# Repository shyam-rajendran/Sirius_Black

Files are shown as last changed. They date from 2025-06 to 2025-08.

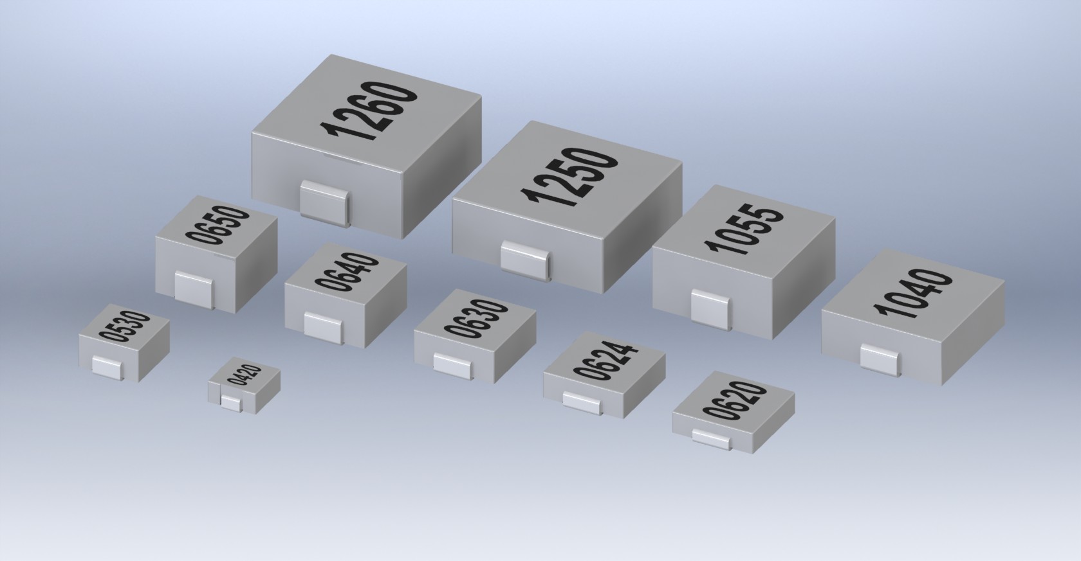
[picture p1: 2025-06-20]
3D Models/SMD Inductors/Inductors.JPG

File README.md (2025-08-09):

# Sirius Black - Flight Computer
<p align="center">
   &nbsp;&nbsp;&nbsp;
  
</p>

Sirius Black is the 5th gen custom flight computer fully designed and developed in house for the sounding rocket built for IREC 25, Airavata. 

Sirius Black consists a multitude of sensors required but not limited for model rocketry, along with 2 integrated pyro channels and 4 servo channels for any actuator control operations. ESP32-S3-N4R8 was the chosen microcontroller due to its great functionalities and prior familiarity with the ESP32 family ICs.

The following write up gives a comprehensive data that could be used while operating with Sirius Black for future projects or serve as reference for any future developements. 

Throughout the developement of this, I documented my approach and considerations I took for most of the steps involved in component selection, schematic design, layout planning, RF considerations, soldering and post-testing results along with mistakes made and solution implemented. My documentation, albeit unstructured, can be found here: 
[Notion](https://chief-cat-5a9.notion.site/Flight-Computer-5-SIRIUS-1274bad4a99a81079046df186ca57ac9)

## Repo Structure
The PCB was designed entirely in Altium Designer. I've included the entire Altium project file including the design files, libraries, 3D models, documentations, schematics, gerber, NCC files. 

To replicate or view the project using Altium, download the files and open it within Altium. Specify the file location for each project file within the project tree.

    1. Sirius FC.DsnWrk 
       The Design Workspace — manages the working environment setup, such as open documents and panels. 
       
    2. Sirius_Black.PrjPcbStructure
       Internal file that manages project structure data, not important.

    3. Sirius_Black.PrjPcb
       The main project file — links all source documents (schematics, PCBs, libraries) and manages project-wide settings.

    4. Sirius_Black.OutJob
       The Output Job file — configures and groups output generation tasks like Gerbers, BOMs, PDFs, etc.

    5. PCB1.PcbDoc
       The PCB layout file — contains the physical board design, footprints, and routing.

    6. Design File (Folder)
        a. MCU.SchDoc
        b. Power Distribution.SchDoc
        c. USB.SchDoc
        d. Sensor Suite 1.SchDoc
        e. Sensor Suite 2.SchDoc
        f. Custom Libraries (folder)
          - Contains all custom or outsourced libraries used within the project.

    7. Libraries (Folder)
        a. Sirius.PcbLib
        b. Sirius.SchLib
        c. Sirius.CMP

    8. Docs (Folder)
       All the datasheets or external PDFs referenced of every component used.

    9. 3D Models (Folder)
       STEP files used for every footprint.

    10. Project Outputs for Sirius_Black (Folder)
        a. Sirius_Black schematics.pdf
        b. Sirius Black.step
        c. BOM.xlsx
        d. Design Rule Check - PCB1.drc
        e. Fabrication Files (Folder)
            i. Final Gerber file used for fabrication
        f. NC Drill (Folder)
            i. Drill files
        g. Gerber (Folder)
            i. Contains the Gerber for all layers individually

    11. Test Codes (Folder)
        All the test codes used while testing.

## Sensor ICs used
- BMI088 (6 Axis Inertial Measurement Unit)
- LSM6DSL (6 Axis Inertial Measurement Unit)
- HMC5883 (3 Axis Magnetometer)
- LIS3MDLTR (3 Axis Magnetometer)
- MS5611 (Temperature and Pressure)
- BMP280 (Temperature and Pressure)
- NEOM8N (Gloabal Navigation Sattelite System)
- DS3231 (Real Time Clock)
- RFM95W (LoRa Module @ 915MHz)

## Pinout and Address

**_Communication Interface:_**
| **SDA** | **SCL** | **MOSI** | **MISO** | **SCK** |  
| --- | --- | -- | -- | -- |
| GPIO4  | GPIO5  | GPIO12 | GPIO13 | GPIO14 | 

**_I2C Peripheral addresses:_**
| **MS5611** | **BMP280** | **BMI088** | **DS3231RTC** | **LSM6DSL** |  **LIS3MDLTR** | **HMC5883L**|
| --- | --- | -- | -- | -- |-- |--|
| 0x77  | 0x76  | Accel: 0x19, Gyro: 0x69 | 0x68 | 0x6A | 0x1C| 0x1E|

**_SPI Peripherals_**

| **RFM95W (LoRa)** | **GPIO** | **Micro SD Card** | **GPIO** | **W25Q128JVSQ (Flash)** | **GPIO** |
|:---:|:---:|:---:|:---:|:---:|:---:|
| SCK | GPIO14  | SCK |  GPIO14  | SCK |  GPIO14  |
| MISO | GPIO13  | MISO |  GPIO13  | MISO |  GPIO13  |
| MOSI | GPIO12  | MOSI |  GPIO12  | MOSI |  GPIO12  |
| DI0 | GPIO08  | CS |  GPIO15  | CS |  GPIO11  |
| RESET | GPIO09  | - | - | - | - |
| NSS | GPIO10  | - | - | - | - |

_**UART Peripheral: NEOM8N**_
| **TX** | **RX** |
|:---:|:---:|
| GPIO17 | GPIO18 |

_**General Pinout:**_
| **Voltage In** | **Passive Buzzer** |
|:---:|:---:|
| GPIO7 | GPIO16 |

_**Pyro Pinout:**_
| **Pyro Channel** |  **GPIO**  |
|:---:|:---:|
| Pyro1 Continuity | GPIO41 |
| Pyro1 Trigger | GPIO48 |
| Pyro2 Continuity | GPIO42 |
| Pyro2 Trigger | GPIO47 |

## Mistakes in Design
1. Made a mistake while creating the footprint for WS2812B LED, where the pins are flipped, essentially rendering this LED as useless.

> No possible solution other that hardwiring it, which I’d rather not do.

2. SD Card not working consistently.
> I’ve implemented every possible solution I could think of yet I couldn’t get it to work properly. The footprint is correct and there is good continuity between all the pins. The SPI channel is healthy as well and does respond to other SPI peripherals.

> What I noticed was the the assigned CS pin fixed at 3V3. Ideally whenever SD card is accessed, CS should be pulled down but for some reason that wasn’t happening. There was no problem with the ESP32 S3 IC itself and the SD card mount was working properly as well.

> Despite checking multiple times for soldering issue or continuity issue I couldn’t find any. However, I noticed that one shell pin (GND) of the mount was not soldered, so I applied solder to it and the SD card started to work only to fail after reaching the US. Unsoldered GND cannot be the issue as out of the 5 GND pins, 4 were properly soldered and there was stable 3V3 supply.

3. W25Q128JVSQ External Flash not responding
> The device address that the flash was returning didn’t correspond to the address as described by the manufacturer. Likely a counterfeit chip.

## Troubleshoot
1. The resistors used across comparator within the pyro channels were modified to change the reference voltage. The capacitor was replaced with a resistor. Input values changed to meet the common mode input voltage requirement. (Check [Notion Page](https://chief-cat-5a9.notion.site/Flight-Computer-5-SIRIUS-1274bad4a99a81079046df186ca57ac9?source=copy_link) for config details)
> Capacitor is changed as because of it the value of IN- doesn’t vary despite changing the resistor in series. This is because the resistor doesn’t have any reference to the ground as the capacitor is in the middle. Changed capacitor to 5.1k

## References
A lot of references and design recommendations were adopted from multiple sources. Selection of key references are listed below.
- [Ublox Hardware Integration Manual](https://content.u-blox.com/sites/default/files/NEO-M8_HardwareIntegrationManual_%28UBX-13003557%29.pdf)
- [ESP32 S3 official documentation](espressif.com)
- [tooyipjee - Spark Analyzer](https://github.com/tooyipjee/Spark-Analyzer/blob/master/pcb/Spark-Analyzer/production/Schematic.pdf)
- [GPS Layout shielding](https://www.youtube.com/watch?v=AJ8TMgo7eG0&t=1245s)
- [Hierarchical Design](https://www.youtube.com/watch?v=eyPB0uBUOnc)
- [hxtec - esp32s3](https://github.com/hxelec/s3p/blob/main/S3P%20schematic.pdf)
- [Imperial Space Society](https://github.com/ImperialSpaceSociety/Flight-Computer/tree/master)
- [GreatScott YouTube](https://www.youtube.com/@greatscottlab)
- [Robert Feranec YouTube](https://www.youtube.com/@RobertFeranec_) (Highly Recommended)
- [Hans Rosenberg YouTube](https://www.youtube.com/@HansRosenberg74)
- [Altium Academy YouTube](https://www.youtube.com/watch?v=yK1qCWjPA-o&list=PLqBNxK9BgJkbIjCz92jbC-2v_DuTPHidB&index=20) (Highly Recommended)
- [Phill's Lab YouTube](https://www.youtube.com/watch?v=_Hfzq1QES-Q&list=PLqBNxK9BgJkbIjCz92jbC-2v_DuTPHidB&index=13) (Highly Recommended)

Author: Shyam Rajendran (monkee)

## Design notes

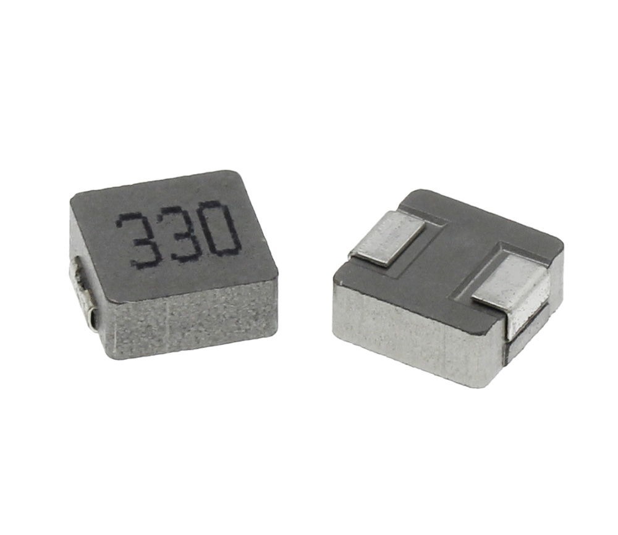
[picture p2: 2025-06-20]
3D Models/SMD Inductors/AMPLF-MPC-ASPI.jpg

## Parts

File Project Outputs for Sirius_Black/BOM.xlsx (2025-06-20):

Comment | Description | Quantity | Designator | Footprint | LibRef
3V | CR2032 Button Cell | 1 | B1 | Battery Holder | Button Cell
0.1uf/100nf | 0.1 uF, Multilayer Ceramic Capacitor, 50 V, ï¿½ 10%, X7R, 0805 [2012 Metric] | 27 | C1, C4, C5, C8, C12, C14, C17, C20, C21, C24, C25, C26, C27, C28, C29, C30, C31, C32, C33, C34, C35, C36, C37, C39, C43, C46, C47 | 0.1uF Capacitor | CC0805KRX7R9BB104
1uF | 1uF, Ceramic Capacitor, Multilayer, Ceramic, 10V, 10% +Tol, 10% -Tol, X7R, 15% TC,Surface Mount, 0805 | 6 | C2, C3, C6, C15, C38, C44 | 10uf Capacitor | CC0805KKX7R6BB105
22uF | CL21A226KOQNNNE-Samsang-16V 22uF X5R ±10% 0805 Multilayer Ceramic Capacitors MLCC – SMD/SMT ROHS | 8 | C7, C9, C10, C11, C16, C18, C22, C23 | 10uf Capacitor | 22uF Capacitor
10uF | 10uF, Multilayer Ceramic Capacitor, 25 V, ï¿½ 10%, X5R, 0805 [2012 Metric] | 2 | C13, C19 | 10uf Capacitor | GRM21BR61E106KA73L
4.7uF | 0603, 25V | 1 | C40 | 1k 0805 Resistor | 4.7uF Capacitor
3.3pF | 0402 | 2 | C41, C42 | 3.3pF | 3.3pF Capacitor
10nF | TCC0402X7R103J500AT-CCTC-SMT ceramic capacitors 0402 X7R 103J(10nF)±5.0% Rated voltage:50V thickness:0.50mm tape | 1 | C45 | 3.3pF | 10nf Capacitor
Blue, 0805 | Blue, 0805 | 4 | D1, D2, D12, D13 | led blue | LED Blue
TVS, SMBJ7.5CA | SMBJ Series 5 W 9.21 V Bi-Directional Surface Mount TVS Diode - SMB | 3 | D3, D4, D5 | TVS Diode | SMBJ7.5CA
BAT54HT1G | BAT54HT1G-ONSEMI-BAT54HT1G-Small Signal Schottky Diode, Single, 30 V, 200 mA, 800 mV, 600 mA, 150 °C | 4 | D6, D7, D8, D11 | SOD2513X110N | BAT54HT1G
RED, 0805 | RED, 0805 | 2 | D9, D10 | led red | LED RED
1kOhm 10MHz | Ferrite Beads Multi-Layer 1KOhm 25% 100MHz 600mA 270mOhm DCR 0805 T/R | 1 | FB1 | 1kOhm Ferrite bead 0402 | BLM21AG102SN1D
Type-C | USB Connector, 16 Contact(s), Female, Right Angle, Surface Mount Terminal, Locking, Receptacle | 1 | J1 | Type C | Type-C
4 Pin JST | Board Connector, 4 Contact(s), 1 Row(s), Male, Straight, Solder Terminal, | 1 | J2 | JST_B4B-XH-A | B4B-XH-A-JST
XT30U-F | XT30U-F | 1 | J3 | XT30UPB-F | XT30 Connector
Micro SD Card | Micro SD Card Connector, 9 Positions, Connector and Ejector, Push In, Auto Eject Out, Surface Mount, 1.8 mm Height Above Board, Gold Flash | 1 | J4 | Micro SD Card | Micro SD Card
3Pin Header |  | 5 | J5, J9, J10, J12, J13 | 3 Pin Header | Header 3pin
Screw terminal | 5.08 pitch | 1 | J6 | Screw terminal | screw terminal
U.fl | ufl connector | 2 | J7, J11 | U.fl | U.fl
SMA | Straight SMA Connector | 1 | J8 | SMA_CONNECTOR | SMA_CONNECTOR
2.2uH | SWPA4030S2R2MT-Sunlord-2.2uH 2.95A 20% 39mOhm Shielded Wirewound Power Inductor SMD | 1 | L1 | SWPA4030S | 2.2uH Inductor
3.3uH | SWPA5020S3R3MT-Sunlord-3.3uH 2.5A 20% 56mOhm Shielded Wirewound Power Inductor SMD | 1 | L2 | SWPA5020 | 3.3uH Inductor
10nH | 0402 | 1 | L3 | 0402 10nH | 10nH Inductor
Green | Green 0805 | 1 | L4 | LED Green | LED Green
27nH | 0402 | 1 | L5 | 0402 10nH | 27nH Inductor
PMH 3.0 | PMH 3.0mm | 4 | MH1, MH2, MH3, MH4 | PMH | PMH
NPN SS8050-G | Trans Gp Bjt NPN 25V 1.5A 300MW 3-PIN SOT-23 T/r | 3 | Q1, Q2, Q4 | Transistor_SS8050-G | SS8050-G
SL2P10A | MOSFET, Power,P-Ch,VDSS -20V,RDS(ON) 0.031Ohm,ID -3.7A,TO-236 (SOT-23),PD 0.75W | Siliconix / Vishay SI2323DS-T1-E3 | 1 | Q3 | P Mosfet SL2P10A | SL2P10A
WNM2021 | WNM2021-Slkor-20V 2.3A 86mΩ@2.5V,1A 200mW 1.2V 1 N-channel SOT-323 MOSFETs ROHS | 2 | Q5, Q6 | P Mosfet SL2P10A | N Mosfet
10k Ohm | 10 kOhm, SMD Chip Resistor, ï¿½ 1%, 125 mW, 0805 [2012 Metric], Thick Film, General Purpose | 23 | R1, R2, R3, R14, R15, R18, R19, R22, R24, R26, R31, R32, R33, R34, R36, R37, R38, R39, R47, R51, R53, R59, R61 | RESC2013X60X35ML10T20 | RC0805FR-0710KL
0Ohm | 0 Ohm Resistor, Jumper, 0805 [2012 Metric], Thick Film, 125 mW, Surface Mount | 10 | R4, R5, R25, R28, R29, R35, R48, R49, R56, R57 | 1k 0805 Resistor | CRCW08050000Z0EA
5.1k Ohm | 5.1k Ohm, 0805, 0.125W, 150V, 1% +/-Tol, 100ppm/Cel, Surface Mount | 8 | R6, R7, R12, R13, R23, R27, R30, R40 | RESC2012X60N | RC0805FR-075K1L
27Ohm | 27 Ohm, Res Thin Film 0805 1% 1/8W ±50ppm/°C Molded SMD SMD Paper T/R | 4 | R8, R9, R44, R46 | 1k 0805 Resistor | RT0805FRE0727RL
1k Ohm | 1k Ohm, 0805, SMD Chip Resistor , ï¿½ 1%, 125 mW,[2012 Metric], Thick Film, General Purpose | 14 | R10, R11, R16, R20, R42, R45, R50, R52, R54, R55, R58, R60, R62, R63 | 1k 0805 Resistor | RC0805FR-071KL
33.2k Ohm | 0805 | 1 | R17 | 1k 0805 Resistor | 33.2k Ohm
54.9k Ohm | 0805 | 1 | R21 | 1k 0805 Resistor | 54.9k Ohm
22k ohm | 0805 | 1 | R41 | 1k 0805 Resistor | 22k Resistor
15k ohm | 0805 | 1 | R43 | 1k 0805 Resistor | 15k Resistor
SMD Switch | PTS810SJG250SMTRLFS, Keypad Switch, 1 Switches, SPST, Momentary-tactile, 0.05A, 16VDC, 4.9N, Solder Terminal, Surface Mount-straight | 2 | SW1, SW2 | Oval Switch | Oval Switch
ESP32-S3-WROOM-1-N4R8 | SMD Module, ESP32-S3, 4 mb Spi F | 1 | U1 | ESP32-S3-WROOM-1-N4 | ESP32-S3-WROOM-1-N4R8
FT232RL-REEL | USB Bus Controller, CMOS, PDSO28 | 1 | U2 | FP-SSOP-28-IPC_B | FT232RL-REEL
TPS563201DDCR | 4.5 V to 17 V input, 3 A output, synchronous step-down converter in Eco-mode | 2 | U3, U5 | TPS563201DDCR | TPS563201DDCR
HT7833 3V3 Regulator | 3V3 Voltage Regulator | 1 | U4 | HT7833 | HT7833
AMS1117-5V | SOT89 | 1 | U6 | AMS1117, 5V | AMS1117-5V
DS3231 RTC | Real Time Clock (RTC) IC Clock/Calendar - IÂ²C, 2-Wire Serial 8-SOIC (0.154, 3.90mm Width) | 1 | U7 | DS3231 | DS3231
W25Q128JVSIQ 16MB (128Mb) | 16MB (128Mb) Flash, PDSO8 | 1 | U8 | W25Q128JVSIQ | W25Q128JVSIQ TR
BMP280 | BMP280 Absolute Barometric Pressure Sensor for Battery Powered Devices 2 x 2.5mm | 1 | U9 | BMP280 | BMP280
LSM6DSL | Accelerometer, Gyroscope, Temperature, 6 Axis Sensor IÂ²C, SPI Output | 1 | U10 | LSM6DSO32TR | LSM6DSL
MS5611 | Sensor;MS5611-BT M-CAPS 3X5X1MM T&R;Pressure;MS561101BA03-50 | TE Connectivity MS561101BA03-50 | 1 | U11 | MS561101BA03-50 | MS561101BA03-50
BMI088 | High-performance 6-axis inertial sensor (accelerometer + gyroscope) <a href="https://pricing.snapeda.com/parts/BMI088/Bosch%20Sensortec/view-part?ref=eda">Check prices</a> | 1 | U12 | BMI088 | BMI088
WS2812B, 5050 | Intelligent Control LED Integrated Light Source, 3.5 to 5.3 V, -25 to 80 degC, 4-Pin SMD, RoHS, Tape and Reel | 1 | U13 | WS2812B | WS2812B
RFM95W-915S2 | RFM95(W) - Low Power Long Range Transceiver Module V1.0 | 1 | U14 | RFM95W-915S2 | RFM95W-915S2
HMC5883L-TR | Board Mount Hall Effect / Magnetic Sensors Sensors, Transducers Magnetic - Hall Effect, Digital Switch, Linear, Compass (ICs) - IC COMPASS 3 AXIS I2C 16LCC SMD | 1 | U15 | HMC5883L-TR | HMC5883L-TR
LIS3MDLTR | Magnetoresistive Sensor X, Y, Z Axis 12-LGA _2x2_ | 1 | U16 | LIS3MDLTR | LIS3MDLTR
Passive Buzzer | 7.5 mm, 3.6 Vo-p, 80 dB, Surface Mount (SMT), Magnetic Audio Transducer Buzzer | 1 | U17 | BuzzerCMT-7525-80-SMT-TR | Buzzer CMT-7525-80-SMT-TR
NEO-M8N-0 | Ic Receiver Gps/Gnss 24lcc | 1 | U18 | NEO-M8N-0 | NEO-M8N-0
MAX9075 | Comparator MAX9075 SOT23-5 | 2 | U19, U20 | Comparator MAX9075 | Comparator MAX9075

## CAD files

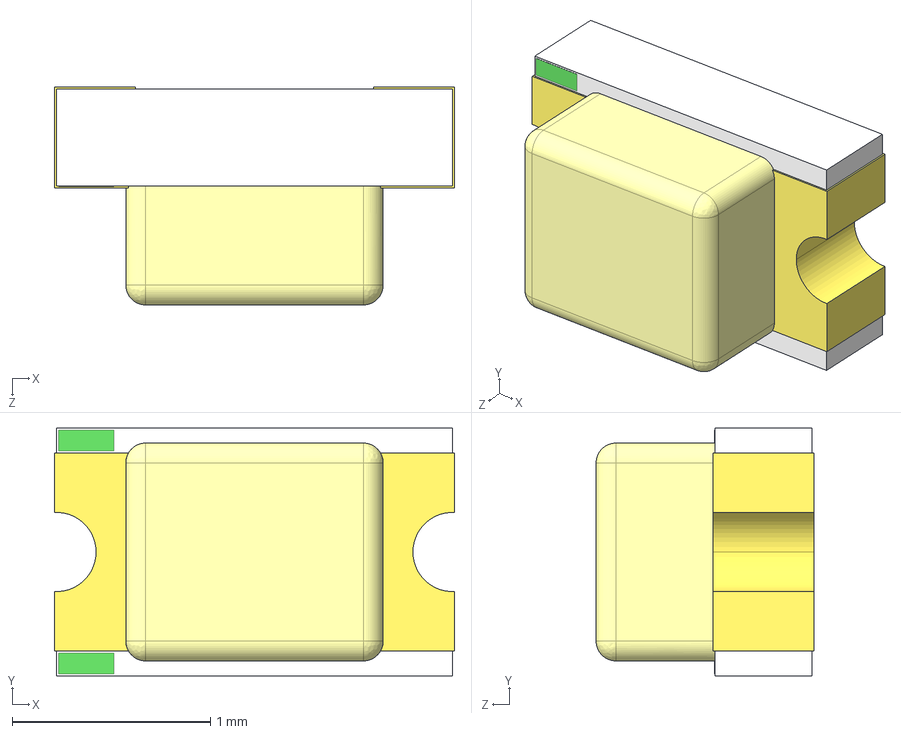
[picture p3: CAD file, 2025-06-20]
3D Models/0805-smd-led-1.snapshot.1/SMD_0805LED_YEL.STEP
2.02 x 1.25 x 1.10 mm

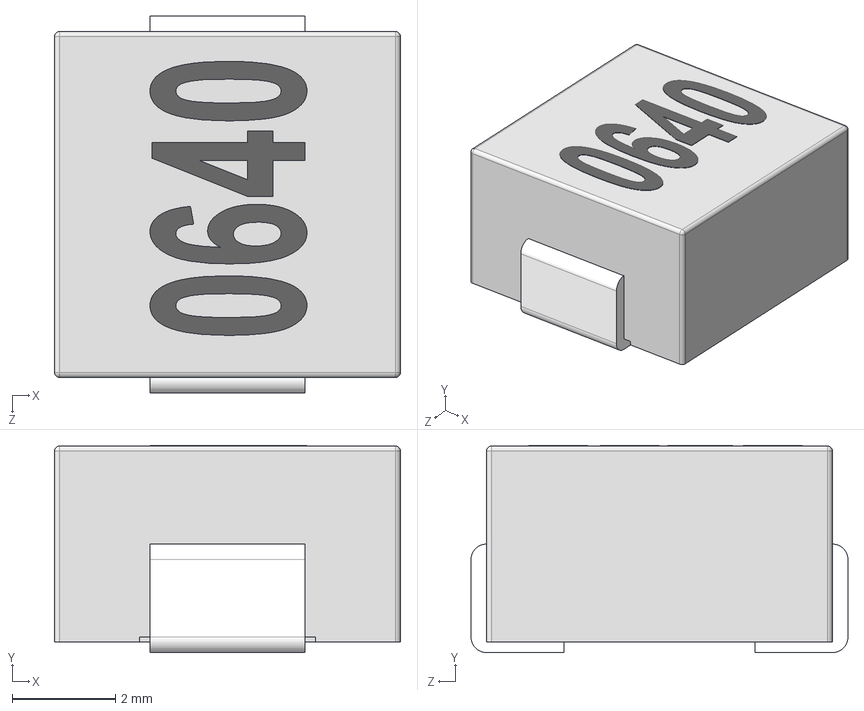
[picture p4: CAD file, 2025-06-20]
3D Models/SMD Inductors/STEP/Inductor_SMD_AMPLF_0640.STEP
6.70 x 4.01 x 7.30 mm

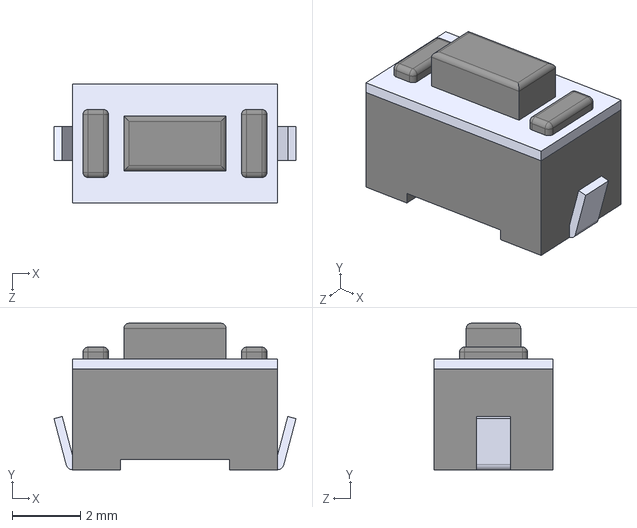
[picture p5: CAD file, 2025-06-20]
3D Models/Switch PTS636 SM43J SMTR LFS.STEP
7.10 x 4.30 x 3.50 mm

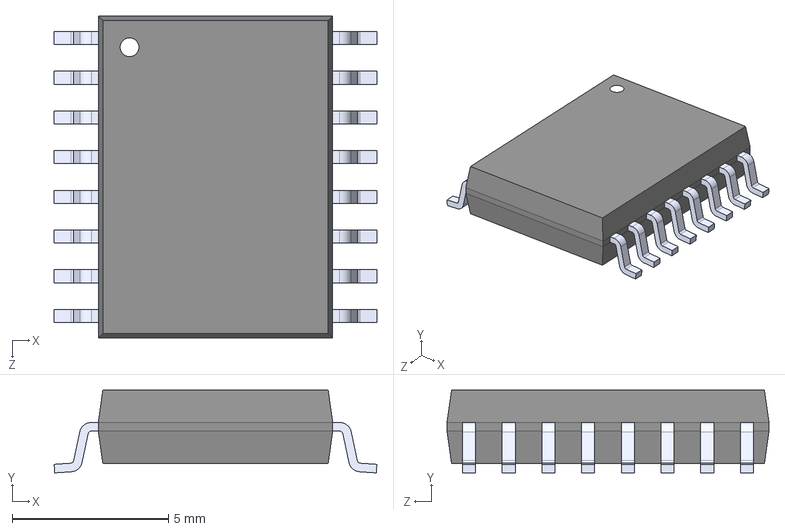
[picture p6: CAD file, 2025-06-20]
3D Models/DS3231.STEP
10.3 x 2.65 x 10.3 mm

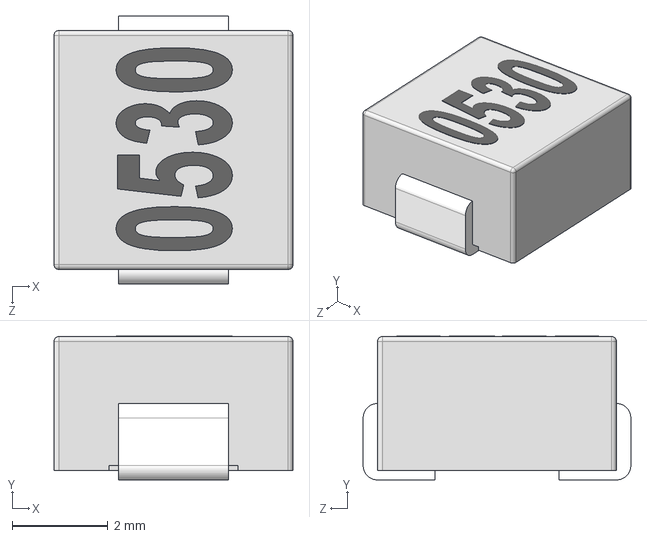
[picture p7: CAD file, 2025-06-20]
3D Models/SMD Inductors/STEP/Inductor_SMD_AMPLF_0530.STEP
5.00 x 3.01 x 5.60 mm

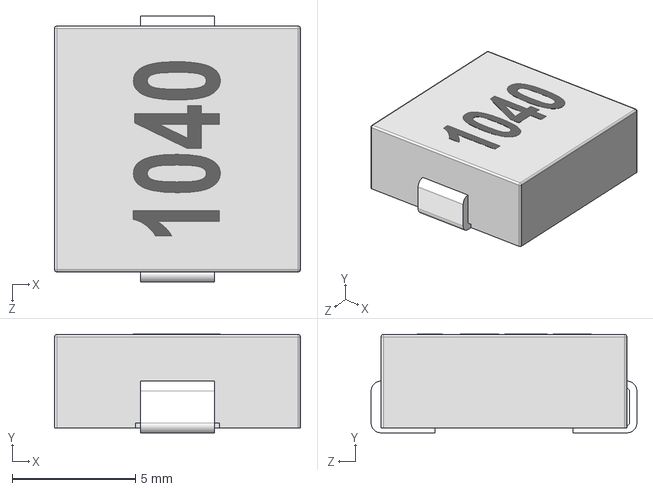
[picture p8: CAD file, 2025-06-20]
3D Models/SMD Inductors/STEP/Inductor_SMD_AMPLF_1040.STEP
10.0 x 4.01 x 10.8 mm

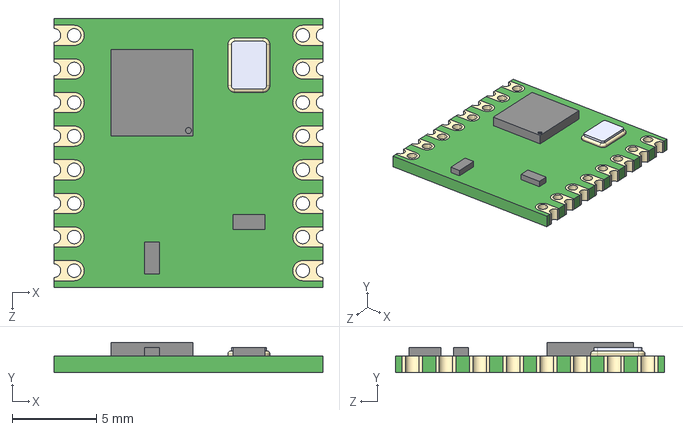
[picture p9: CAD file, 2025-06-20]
3D Models/RFM95W-915S2--3DModel-STEP-56544.STEP
16.0 x 1.80 x 16.0 mm

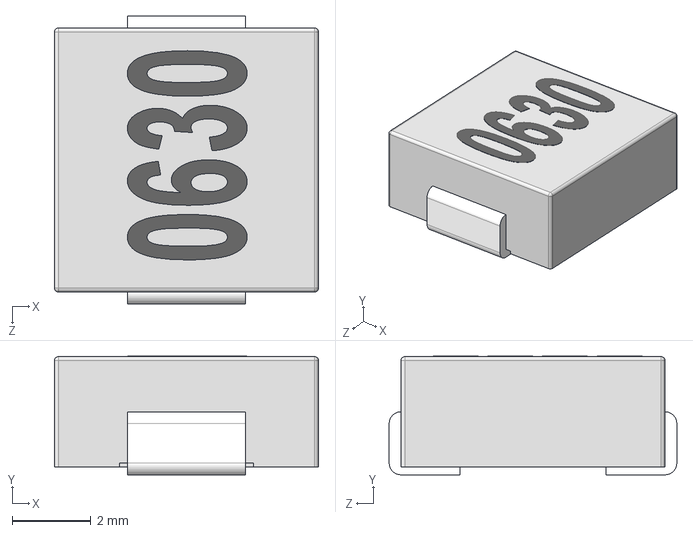
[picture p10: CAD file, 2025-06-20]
3D Models/SMD Inductors/STEP/Inductor_SMD_AMPLF_0630.STEP
6.70 x 3.01 x 7.30 mm

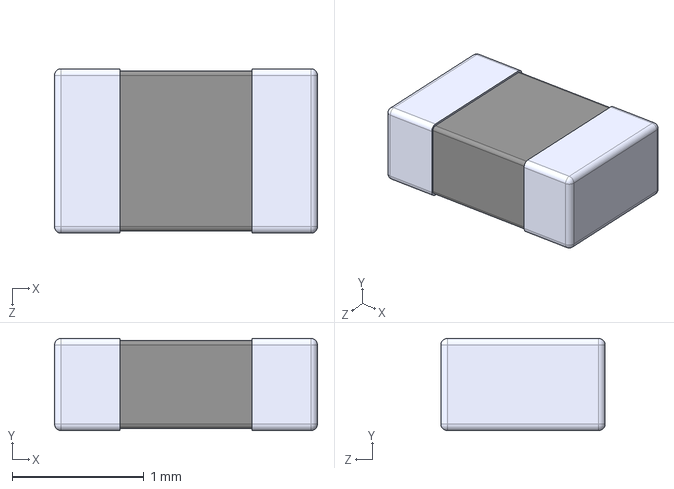
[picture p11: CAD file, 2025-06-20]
3D Models/10uf CC0805KKX5R8BB106.step
2.00 x 0.7 x 1.25 mm

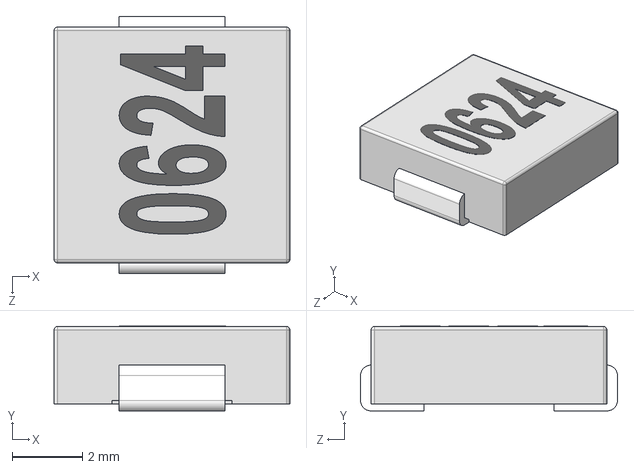
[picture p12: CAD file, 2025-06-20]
3D Models/SMD Inductors/STEP/Inductor_SMD_AMPLF_0624.STEP
6.70 x 2.41 x 7.30 mm

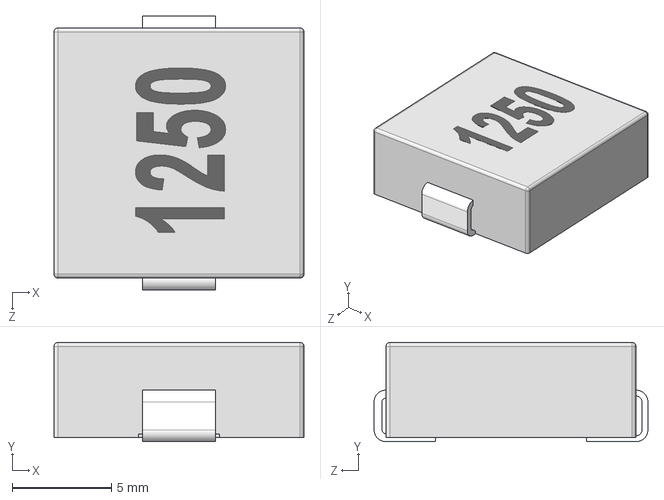
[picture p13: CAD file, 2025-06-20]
3D Models/SMD Inductors/STEP/Inductor_SMD_AMPLF_1250.STEP
12.6 x 5.01 x 13.8 mm

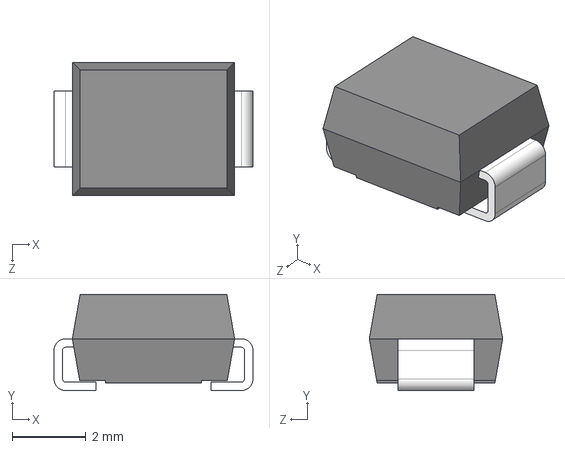
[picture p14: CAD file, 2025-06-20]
3D Models/TVS DIODE SMBJ75CA.step
5.40 x 2.61 x 3.62 mm

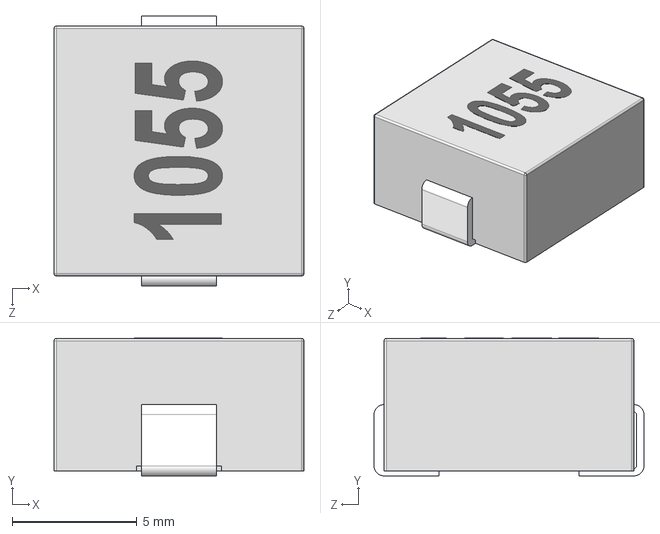
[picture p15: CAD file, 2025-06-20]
3D Models/SMD Inductors/STEP/Inductor_SMD_AMPLF_1055.STEP
10.0 x 5.51 x 10.8 mm

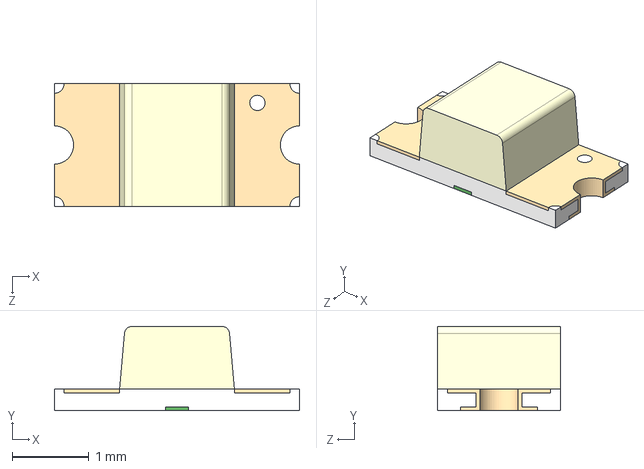
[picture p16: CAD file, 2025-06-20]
3D Models/LED.STEP
3.20 x 1.10 x 1.60 mm

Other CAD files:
3D Models/0805-smd-led-1.snapshot.1/SMD_0805LED_GREEN.STEP
3D Models/0805-smd-led-1.snapshot.1/SMD_0805LED_BLU.STEP
3D Models/0805-smd-led-1.snapshot.1/SMD_0805LED_RED.STEP
3D Models/SMD Inductors/STEP/Inductor_SMD_AMPLF_0650.STEP
3D Models/0402 10nH.STEP
3D Models/0402 ferrite bead.STEP
3D Models/3.3pF 0402.STEP
3D Models/3pin jst.STEP
3D Models/BATTERY Holder.STEP
3D Models/BMI088.step
3D Models/BMP280.step
3D Models/Buzzzer CMT-7525-80-SMT-TR--3DModel-STEP-1.STEP
3D Models/ESP32-S3-WROOM-1-N4.STEP
3D Models/HMC5883L-TR.STEP
3D Models/JST-B4B-XH-A.step
3D Models/LED-0805-green.step
3D Models/LIS3MDLTR.step
3D Models/M7 1N4007.STEP
3D Models/MCP16311-E_MS.STEP
3D Models/MS5611 01BA03-50.step
3D Models/Micro SD Card.STEP
3D Models/NEO-M8N-0.STEP
3D Models/NPN Transistor SS8050-G.step
3D Models/RC0805FR-075K1L.step
3D Models/SMD Inductors/SLDPRT/Inductor_SMD_AMPLF_0420.SLDPRT
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

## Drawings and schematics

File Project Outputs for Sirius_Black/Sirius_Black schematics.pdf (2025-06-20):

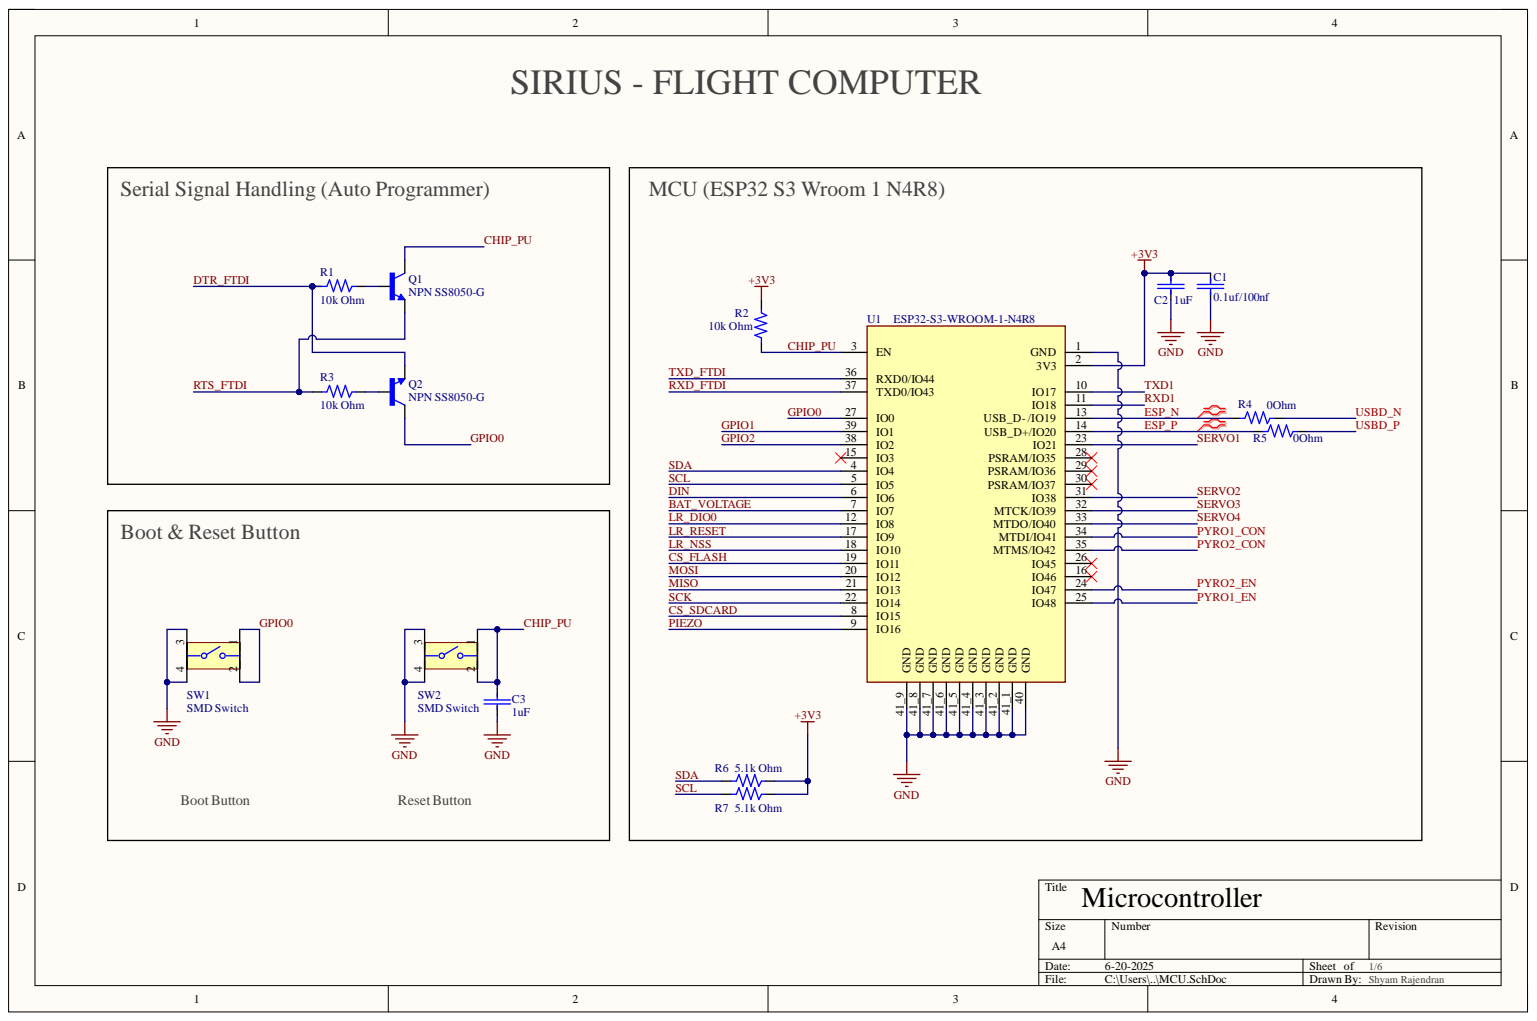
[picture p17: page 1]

GND 40 GND 41_1 GND 41_2 GND 41_3 GND 41_4 GND 41_5 GND 41_6 GND 41_7 GND 41_8 GND 41_9

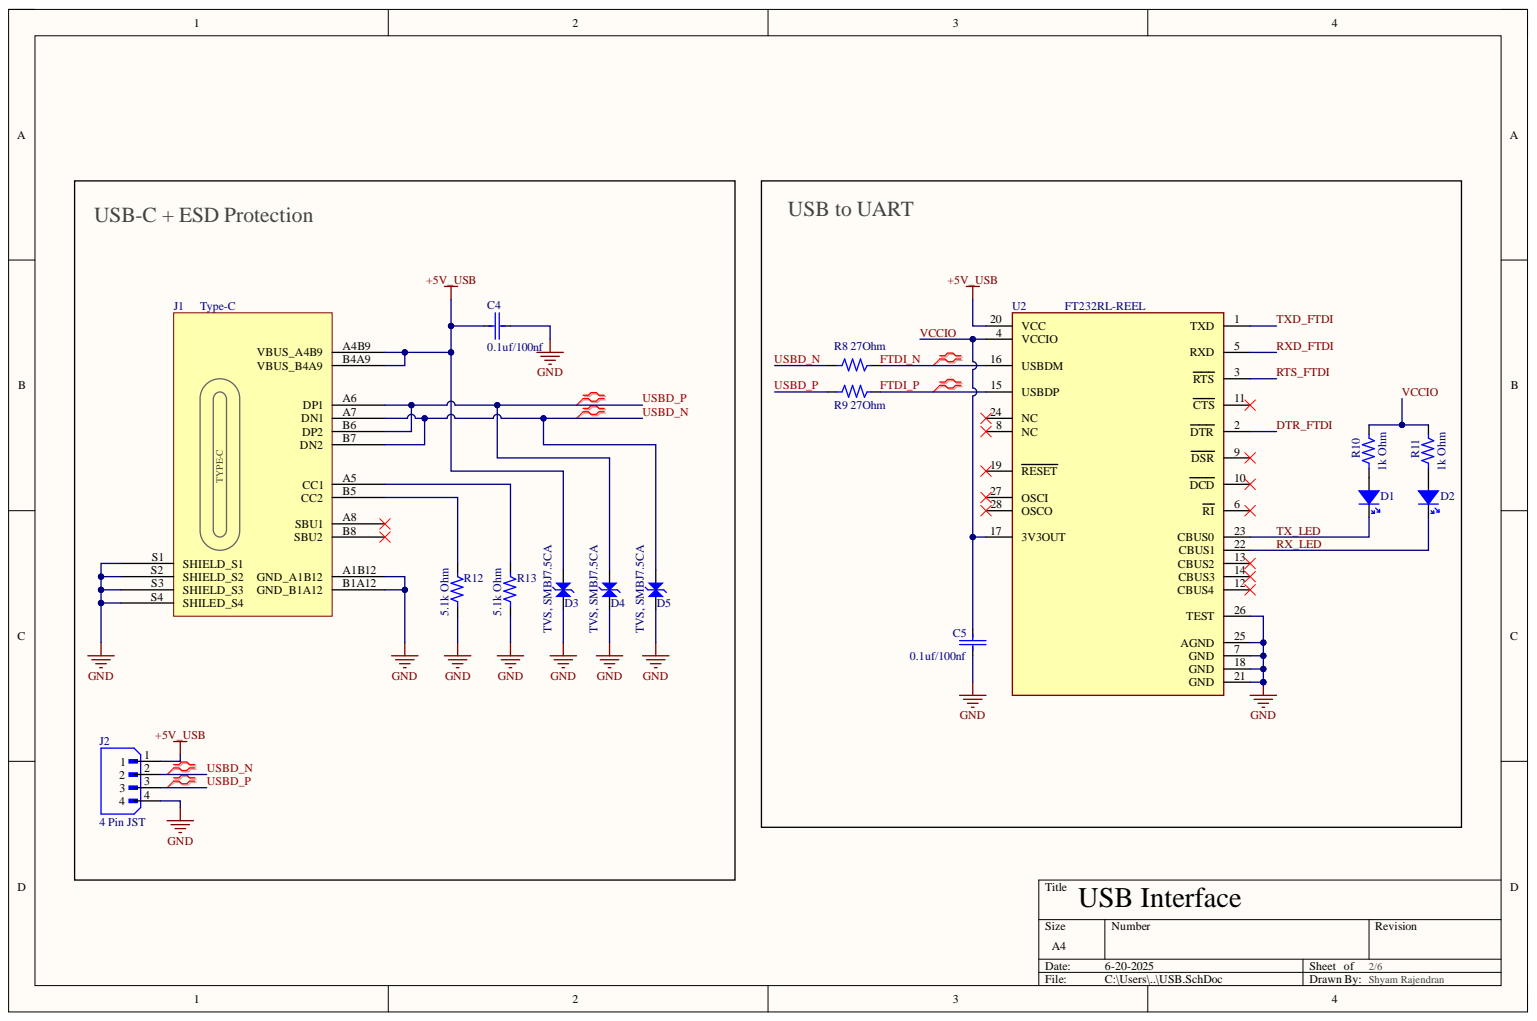
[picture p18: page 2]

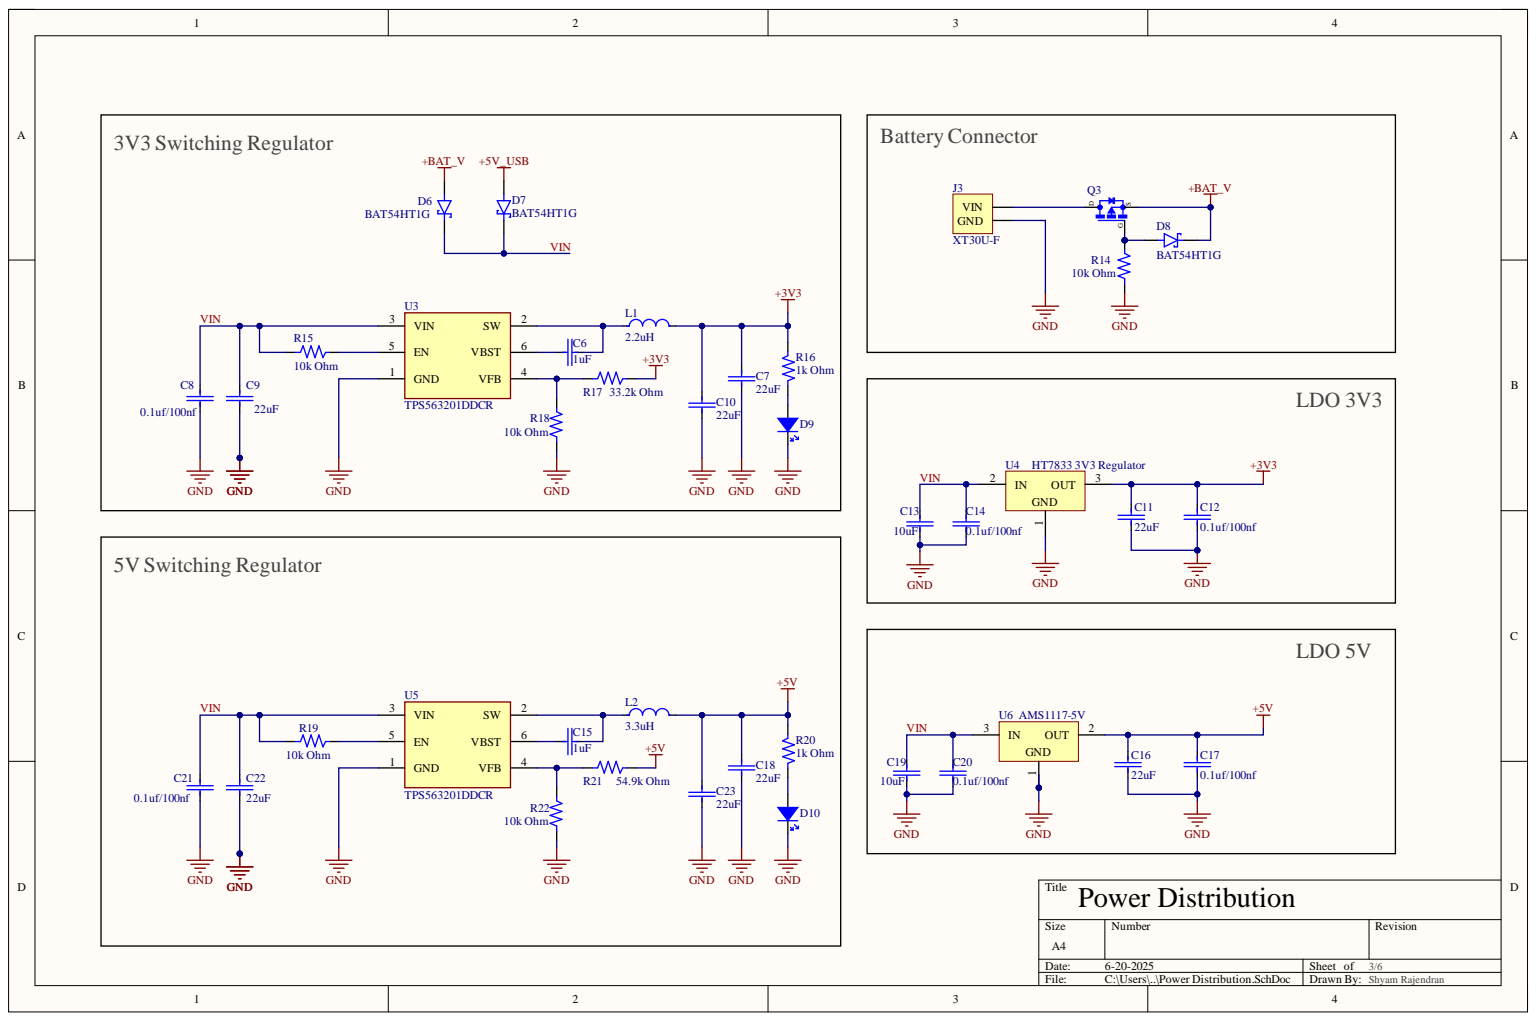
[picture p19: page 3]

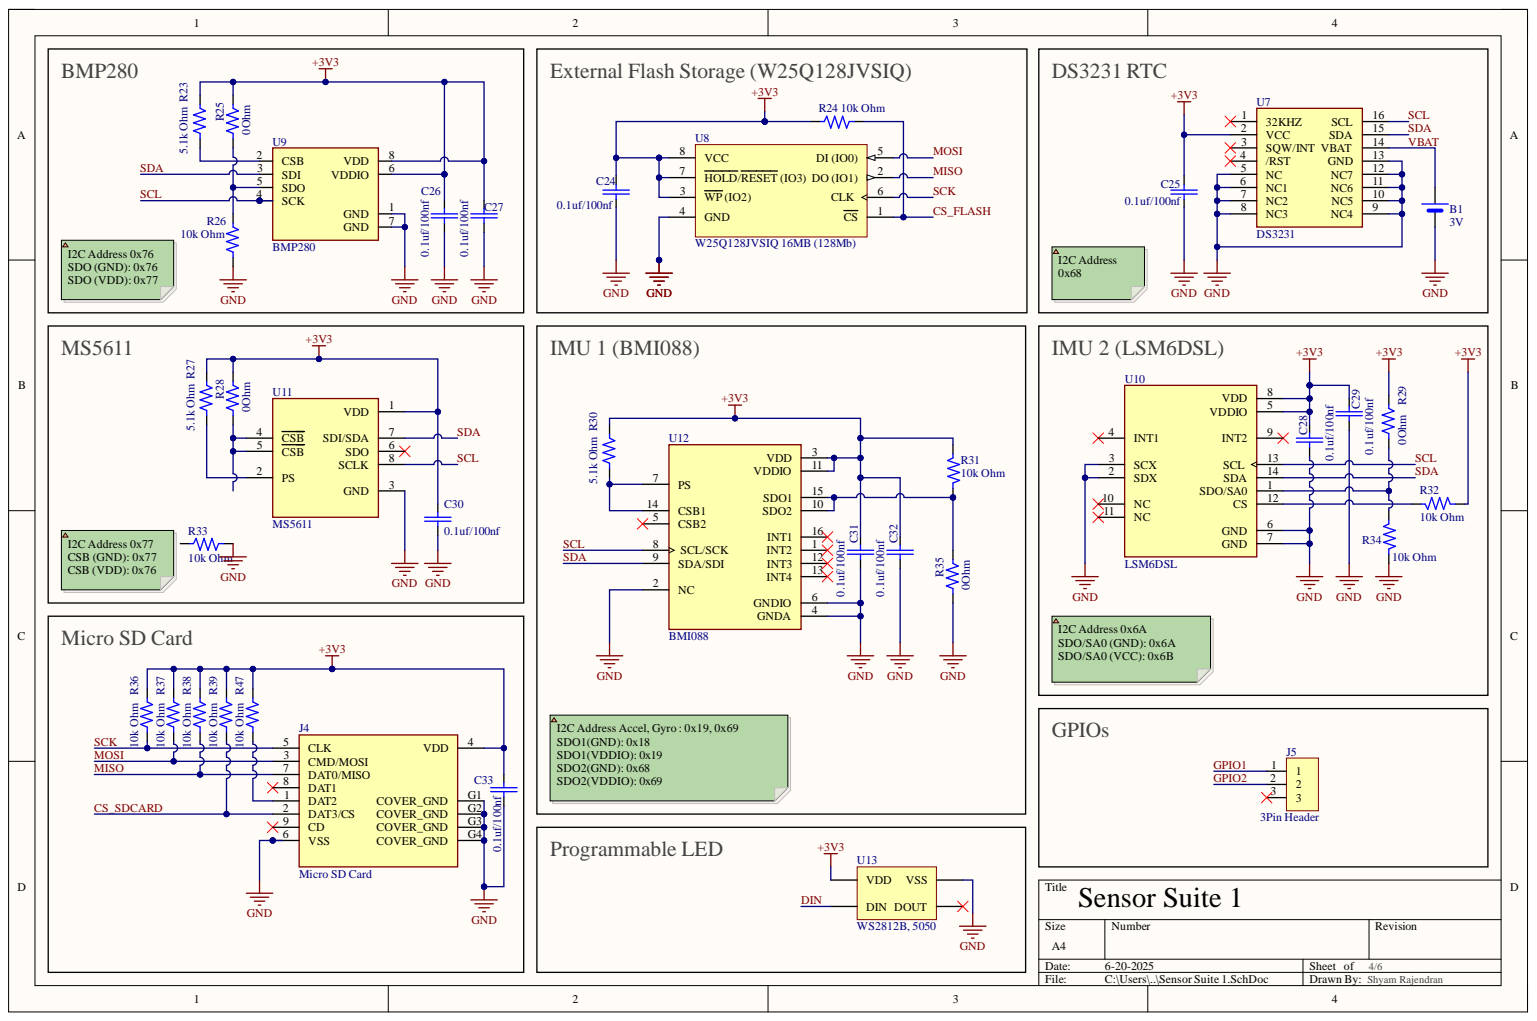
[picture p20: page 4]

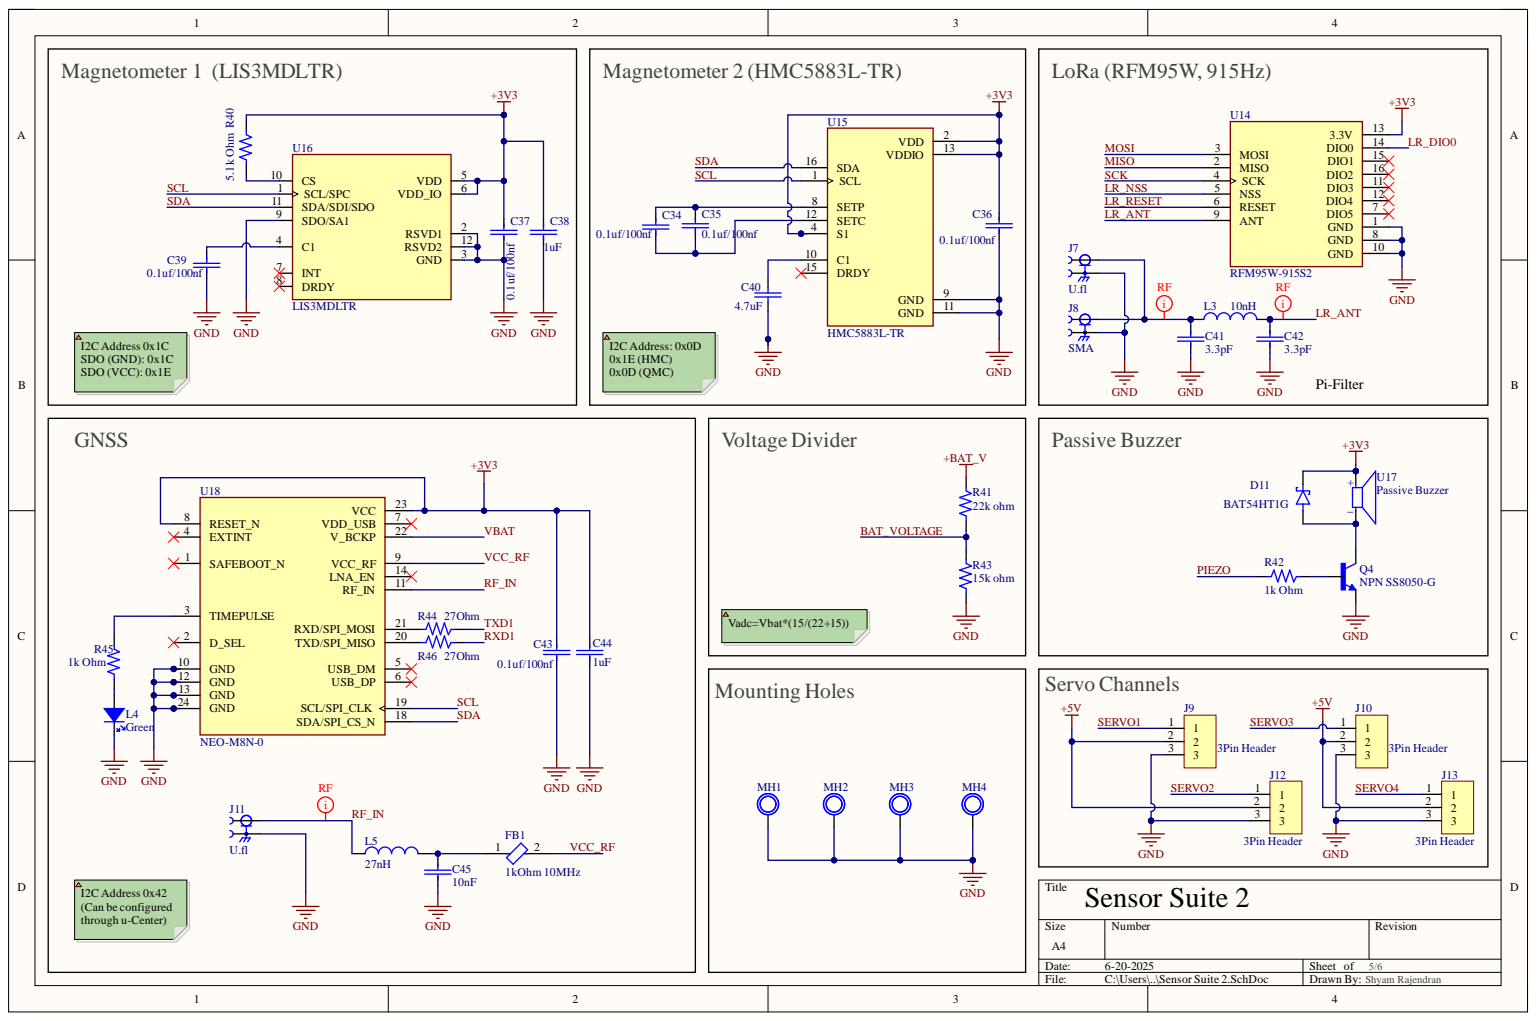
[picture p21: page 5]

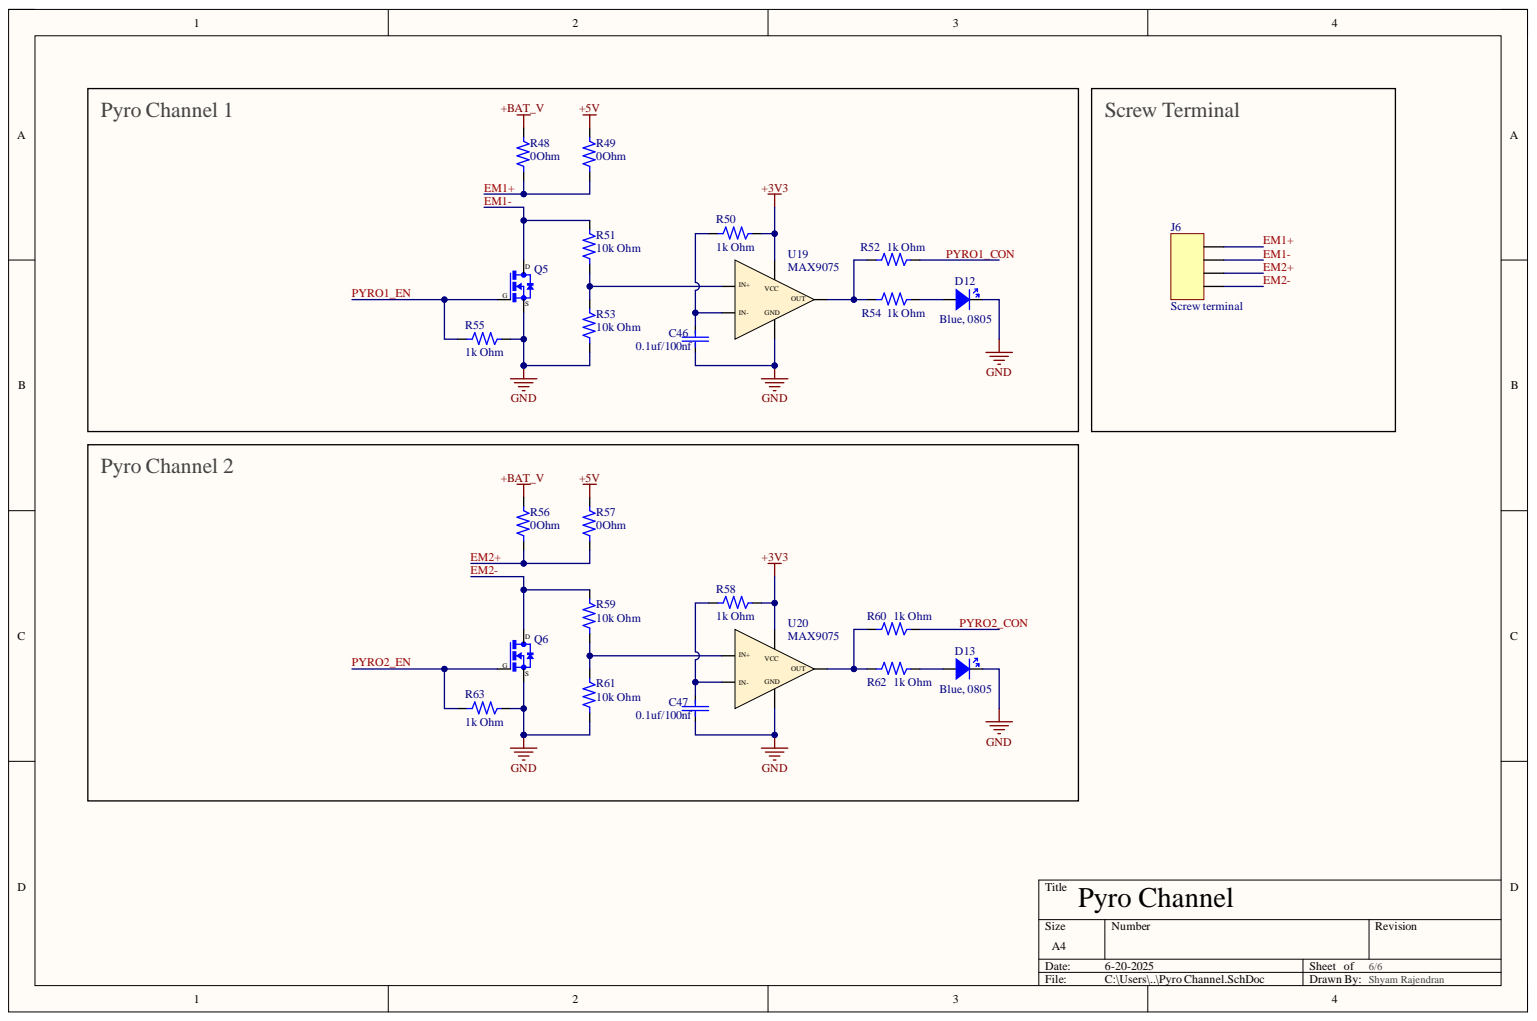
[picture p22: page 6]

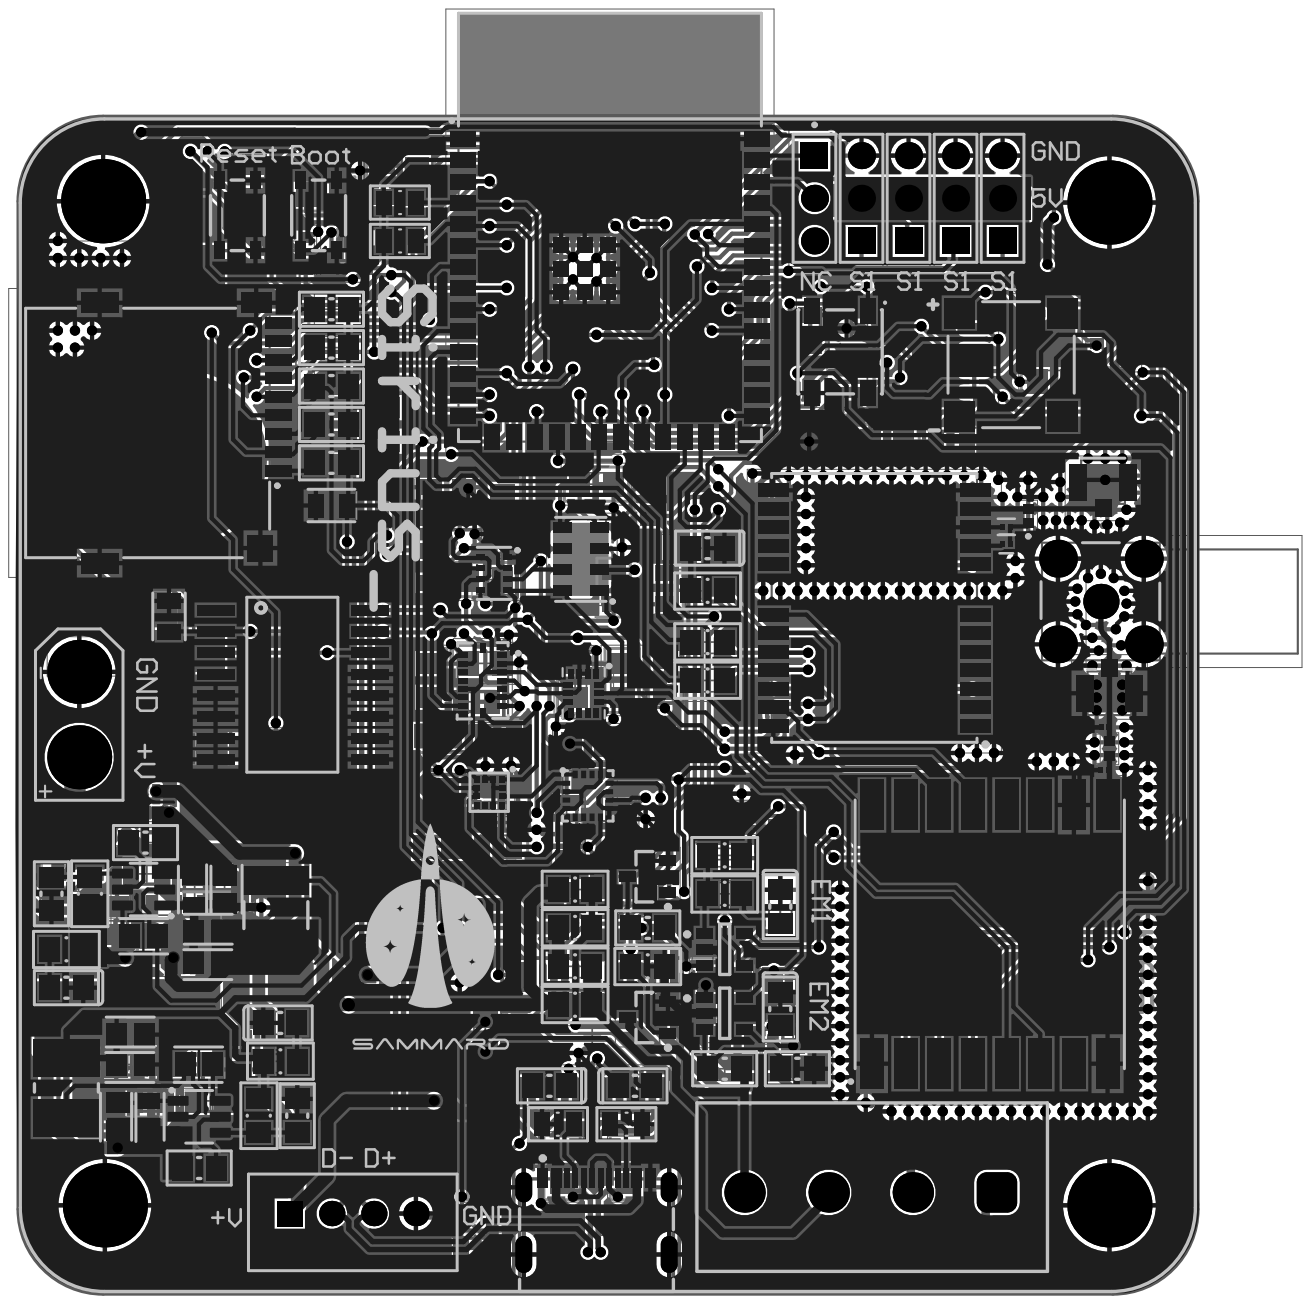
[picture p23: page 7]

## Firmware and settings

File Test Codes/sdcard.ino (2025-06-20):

#include <SPI.h>
#include <SD.h>



// sirius test
#define PIN_SPI_CS   15   // Chip Select pin
#define PIN_SPI_MOSI 12  // MOSI
#define PIN_SPI_MISO 13  // MISO
#define PIN_SPI_SCLK 14  // SCLK

int packetCount = 0;  // Declare globally so loop() can access it

void setup() {
    Serial.begin(115200);
    while (!Serial); // Wait for Serial Monitor (for debugging)

    Serial.println("Initializing SD card...");

    // Initialize SPI with custom pins
    SPI.begin(PIN_SPI_SCLK, PIN_SPI_MISO, PIN_SPI_MOSI, PIN_SPI_CS);

    // Try to initialize SD card
    if (!SD.begin(PIN_SPI_CS)) {
        Serial.println("SD card initialization failed!");
        Serial.println("Possible causes:");
        Serial.println("- Incorrect wiring (check CS, MOSI, MISO, SCLK)");
        Serial.println("- SD card not inserted properly");
        Serial.println("- SD card not formatted as FAT16/FAT32");
        return;
    }
    Serial.println("SD card initialized successfully!");

    // Check if file exists or create it
    if (SD.exists("/data.csv")) {
        Serial.println("data.csv already exists.");
    } else {
        Serial.println("Creating data.csv...");
        File file = SD.open("/data.csv", FILE_WRITE);
        if (file) {
            file.println("TEAM_ID,TIME,PACKET_COUNT,MODE,STATE,ALTITUDE,TEMPERATURE,PRESSURE,VOLTAGE," // Header row
                         "GYRO_R,GYRO_P,GYRO_Y,ACCEL_R,ACCEL_P,ACCEL_Y,MAG_R,MAG_P,MAG_Y,AUTO_GYRO_ROT_RATE,"
                         "GPS_TIME,GPS_ALTITUDE,GPS_LATITUDE,GPS_LONGITUDE,GPS_SATS,CMD_ECHO,RPM_ONE,RPM_TWO");
            file.close();
            Serial.println("Headers written to data.csv");
        } else {
            Serial.println("Error creating data.csv");
        }
    }
}

void loop() {
    // Simulating random sensor values
    int mode = random(0, 5);
    String currentState = "ACTIVE";
    float altitude = random(100, 500) / 10.0;
    float temperature = random(200, 350) / 10.0;
    float pressure = random(900, 1100);
    float voltage = random(30, 50) / 10.0;

    float gyro_r = random(-100, 100) / 10.0;
    float gyro_p = random(-100, 100) / 10.0;
    float gyro_y = random(-100, 100) / 10.0;

    float accel_r = random(-50, 50) / 10.0;
    float accel_p = random(-50, 50) / 10.0;
    float accel_y = random(-50, 50) / 10.0;

    float mag_r = random(-200, 200) / 10.0;
    float mag_p = random(-200, 200) / 10.0;
    float mag_y = random(-200, 200) / 10.0;

    float auto_gyro_rot_rate = random(10, 100) / 10.0;

    float gps_time = millis() / 1000.0;
    float gps_altitude = random(100, 500);
    float gps_latitude = random(-9000000, 9000000) / 100000.0;
    float gps_longitude = random(-18000000, 18000000) / 100000.0;
    int gps_sats = random(4, 12);
    int cmd_echo = random(0, 255);

    int rpm_one = random(1000, 5000);
    int rpm_two = random(1000, 5000);

    // Constructing CSV row
    String data = "TEAM_ID, " + String(millis()) + ", " + String(packetCount++) + ", " + String(mode) + ", " + currentState + ", " +
                  String(altitude) + ", " + String(temperature) + ", " + String(pressure) + ", " + String(voltage) + ", " +
                  String(gyro_r) + ", " + String(gyro_p) + ", " + String(gyro_y) + ", " +
                  String(accel_r) + ", " + String(accel_p) + ", " + String(accel_y) + ", " +
                  String(mag_r) + ", " + String(mag_p) + ", " + String(mag_y) + ", " + String(auto_gyro_rot_rate) + ", " +
                  String(gps_time) + ", " + String(gps_altitude) + ", " + String(gps_latitude) + ", " +
                  String(gps_longitude) + ", " + String(gps_sats) + ", " + String(cmd_echo) + ", " +
                  String(rpm_one) + ", " + String(rpm_two);

    // Open CSV file and write data (append new line)
    File file = SD.open("/data.csv", FILE_APPEND);
    if (file) {
        file.println(data);  // Make sure each entry is on a new line
        file.close();
        Serial.println("Data written to SD card: " + data);
    } else {
        Serial.println("Error opening CSV file for writing.");
    }

    delay(2000); // Log data every 2 seconds
}

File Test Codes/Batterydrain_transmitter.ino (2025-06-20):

#include <SPI.h>
#include <LoRa.h>
#include <Wire.h>
#include <Adafruit_BMP280.h>
#include <MS5611.h>
#include <TinyGPSPlus.h>

// LoRa pins
#define LORA_SCK     14
#define LORA_MISO    13
#define LORA_MOSI    12
#define LORA_CS      10
#define LORA_RST     9
#define LORA_IRQ     8

#define LORA_FREQ    915E6

// I2C Pins
#define SDA_PIN 4
#define SCL_PIN 5

// Sensor Addresses
#define BMP280_ADDR 0x76
#define MS5611_ADDR 0x77

// GPS UART Pins
#define GPS_RX 18
#define GPS_TX 17

Adafruit_BMP280 bmp280;
MS5611 ms5611(MS5611_ADDR);
TinyGPSPlus gps;
HardwareSerial GPS_Serial(1);

void setup() {
  Serial.begin(115200);
  GPS_Serial.begin(9600, SERIAL_8N1, GPS_RX, GPS_TX);

  Wire.begin(SDA_PIN, SCL_PIN);
  bmp280.begin(BMP280_ADDR);
  ms5611.begin();
  ms5611.setOversampling(OSR_ULTRA_HIGH);

  SPI.begin(LORA_SCK, LORA_MISO, LORA_MOSI, LORA_CS);
  pinMode(LORA_RST, OUTPUT);
  digitalWrite(LORA_RST, LOW);
  delay(20);
  digitalWrite(LORA_RST, HIGH);
  delay(20);

  LoRa.setPins(LORA_CS, LORA_RST, LORA_IRQ);
  if (!LoRa.begin(LORA_FREQ)) {
    Serial.println("LoRa init failed");
    while (1);
  }

  LoRa.setTxPower(20, PA_OUTPUT_PA_BOOST_PIN);  // Max power
  Serial.println("✅ LoRa transmitter ready");
}

void loop() {
  // GPS update
  while (GPS_Serial.available()) {
    gps.encode(GPS_Serial.read());
  }

  // Read sensors
  float bmp_temp = bmp280.readTemperature();
  float bmp_press = bmp280.readPressure() / 100.0;
  float bmp_alt = bmp280.readAltitude(1013.25);

  ms5611.read();
  float ms_temp = ms5611.getTemperature();
  float ms_press = ms5611.getPressure();
  float ms_alt = 44330.0 * (1.0 - pow(ms_press / 1013.25, 0.1903));

  // Time for CSV
  char timestamp[16] = "NA";
  if (gps.time.isValid()) {
    snprintf(timestamp, sizeof(timestamp), "%02d:%02d:%02d",
             gps.time.hour(), gps.time.minute(), gps.time.second());
  }

  // Build CSV String
  String csv = String(timestamp) + "," +
               String(bmp_temp, 2) + "," + String(bmp_press, 2) + "," + String(bmp_alt, 2) + "," +
               String(ms_temp, 2) + "," + String(ms_press, 2) + "," + String(ms_alt, 2) + ",";

  if (gps.location.isValid()) {
    csv += String(gps.location.lat(), 6) + "," + String(gps.location.lng(), 6) + ",";
  } else {
    csv += "NA,NA,";
  }

  if (gps.altitude.isValid()) {
    csv += String(gps.altitude.meters(), 2);
  } else {
    csv += "NA";
  }

  // Transmit over LoRa
  LoRa.beginPacket();
  LoRa.print(csv);
  LoRa.endPacket();

  Serial.println("📡 Sent CSV:");
  Serial.println(csv);

  delay(1000);  // Or lower for higher data rate
}
